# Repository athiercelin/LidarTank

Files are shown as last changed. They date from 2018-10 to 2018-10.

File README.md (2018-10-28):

# Lidar Tank

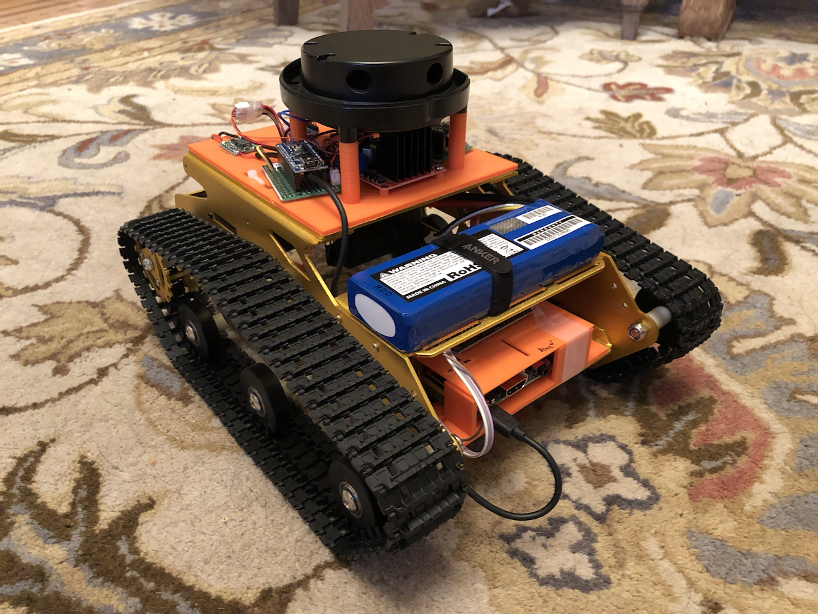
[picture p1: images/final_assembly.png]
Final Product


## Bill of Materials

|Quantity|Picture|Label|Comments|
|---|---|---|---|
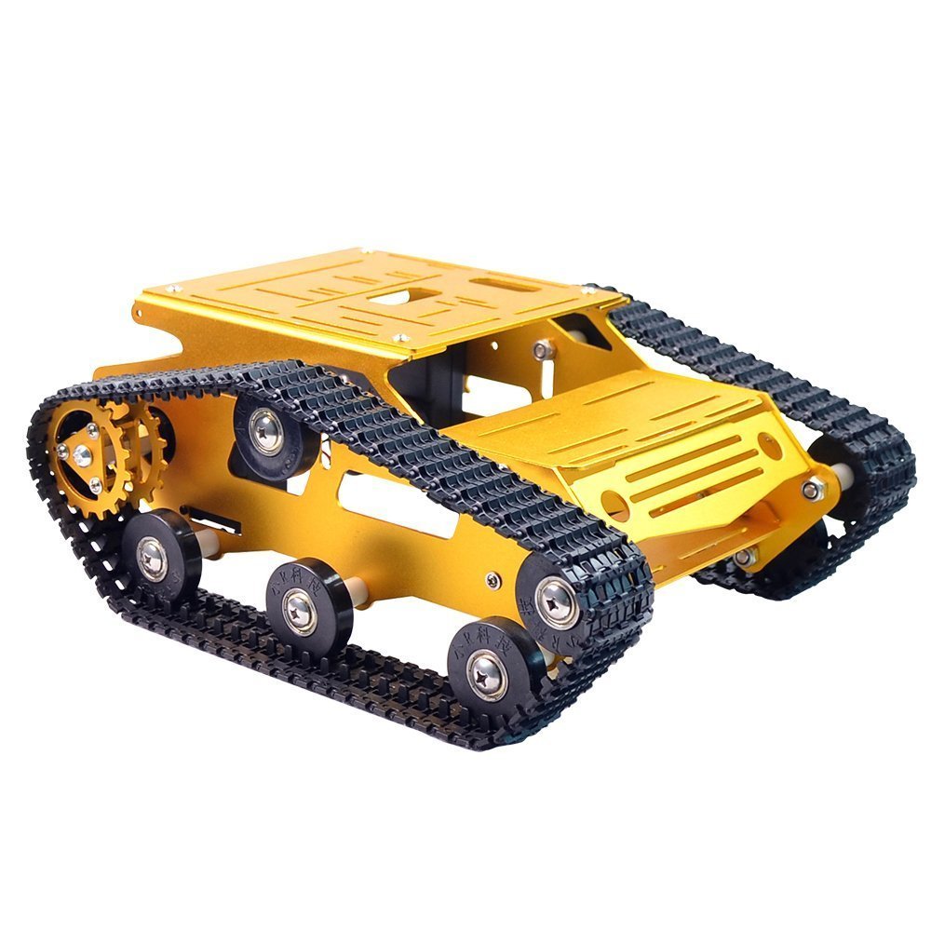
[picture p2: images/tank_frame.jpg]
|1||[Tank Frame](https://www.amazon.com/gp/product/B077Z4GYLB/ref=oh_aui_detailpage_o02_s00?ie=UTF8&psc=1)||
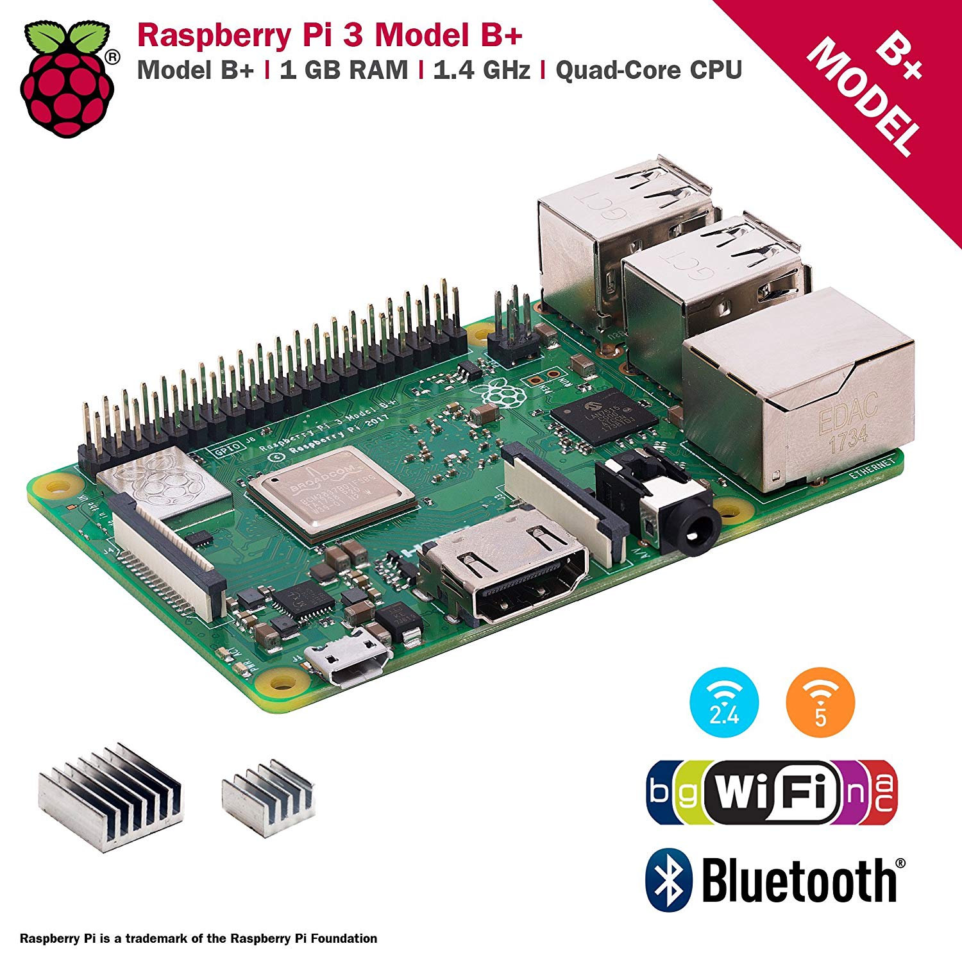
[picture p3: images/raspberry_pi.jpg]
|1||[Raspberry Pi 3+](https://www.amazon.com/gp/product/B07BC6WH7V/ref=oh_aui_detailpage_o02_s00?ie=UTF8&psc=1)||
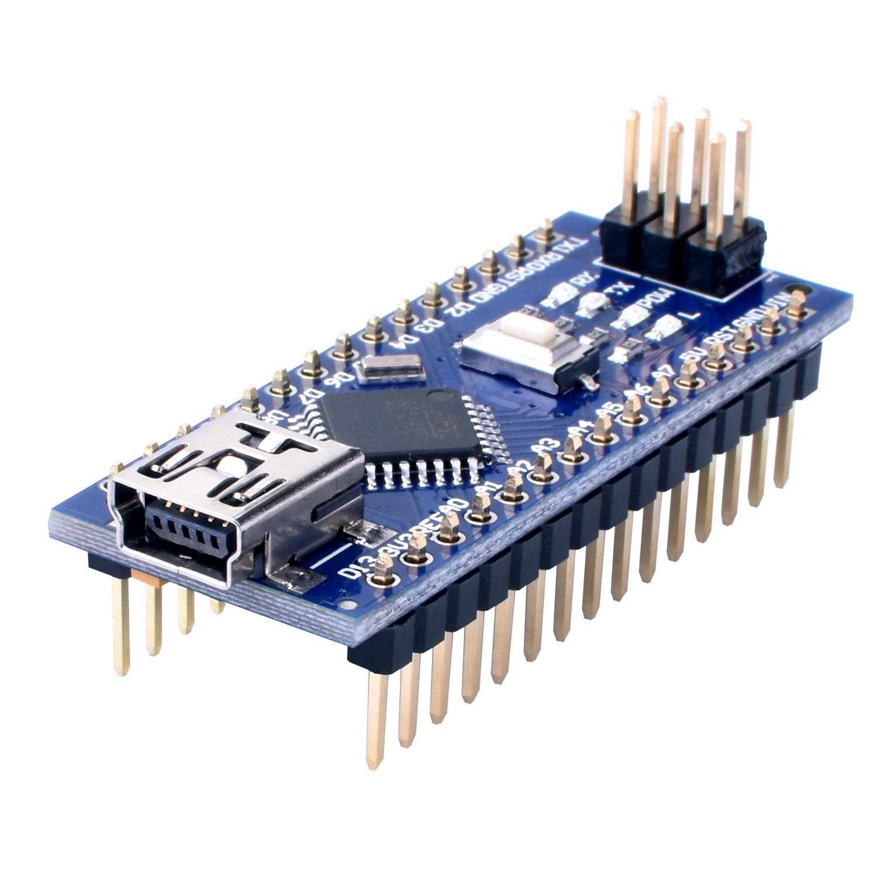
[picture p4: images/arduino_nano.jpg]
|2||[Arduino Nano](https://www.amazon.com/dp/B01MSYWE6B/ref=sspa_dk_detail_2?psc=1&pd_rd_i=B01MSYWE6B)|sd|
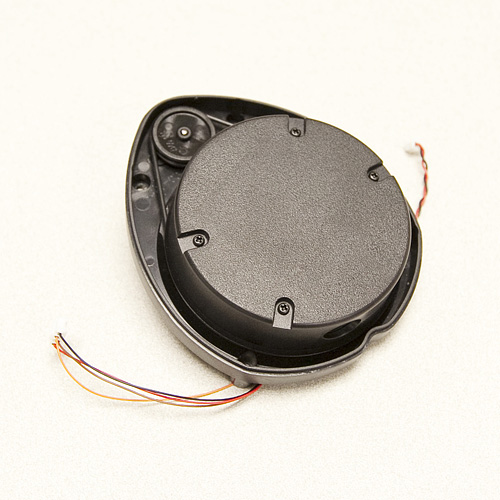
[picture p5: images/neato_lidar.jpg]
|1||Neato Lidar|I got this one for free so I don't have a place to find one easily|
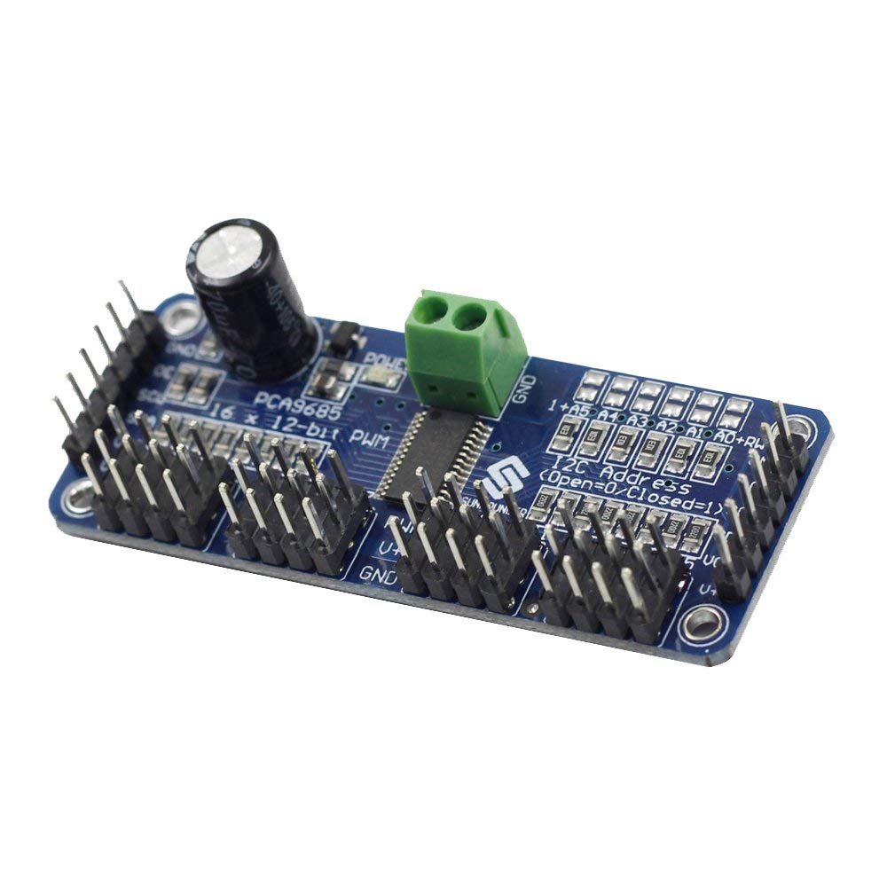
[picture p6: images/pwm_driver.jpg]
|1||[PWM Driver](https://www.amazon.com/gp/product/B014KTSMLA/ref=oh_aui_detailpage_o05_s00?ie=UTF8&psc=1)||
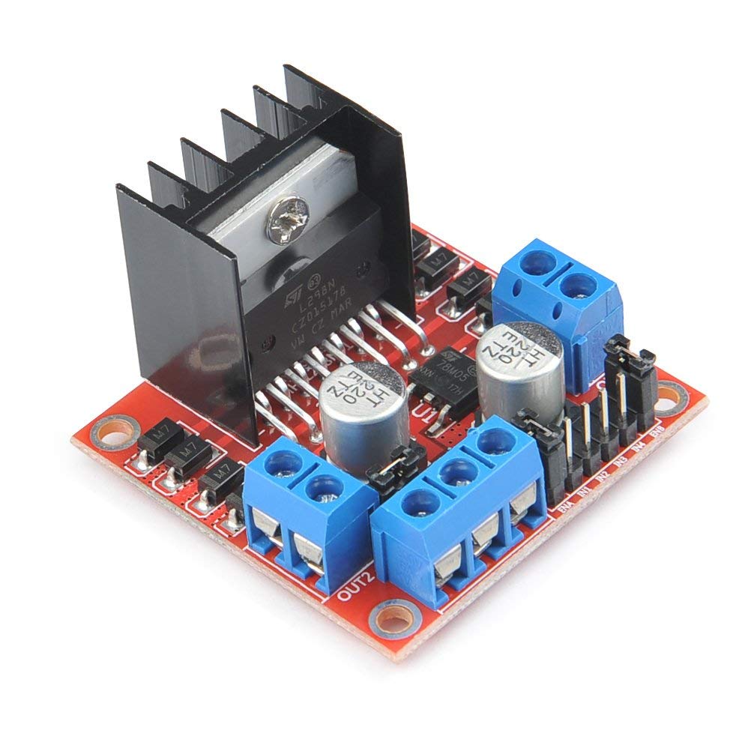
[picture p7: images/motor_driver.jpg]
|1||[Motor Driver](https://www.amazon.com/gp/product/B078D7DR9V/ref=oh_aui_detailpage_o05_s00?ie=UTF8&psc=1)||
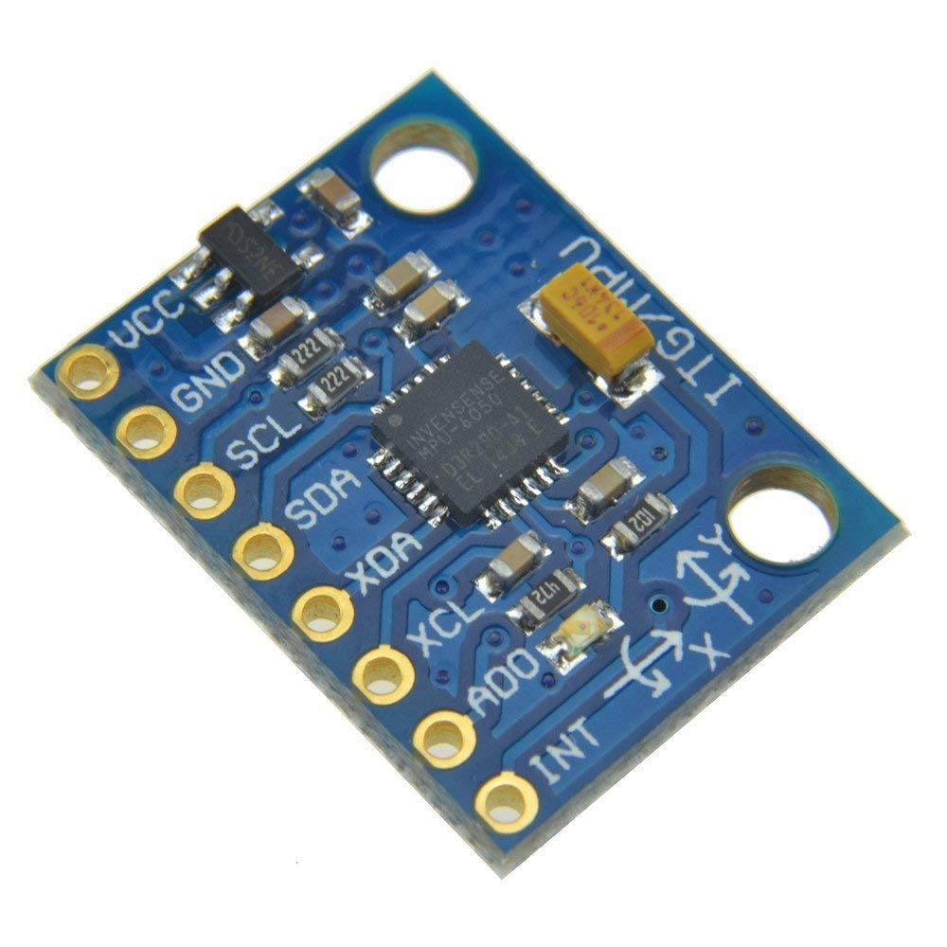
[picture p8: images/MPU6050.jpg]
|1||[MPU6050 IMU](https://www.amazon.com/Diymore-MPU-6050-Gyroscope-Accelerometer-Arduino/dp/B06XVXPZDP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)||
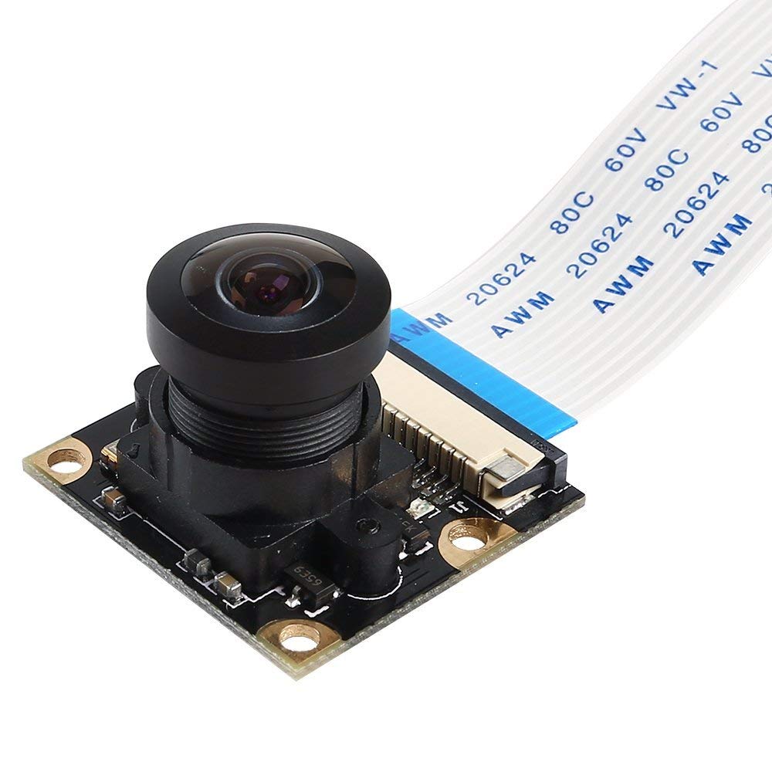
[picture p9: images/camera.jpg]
|1||[Camera module](https://www.amazon.com/gp/product/B00N1YJKFS/ref=oh_aui_detailpage_o00_s00?ie=UTF8&psc=1)||
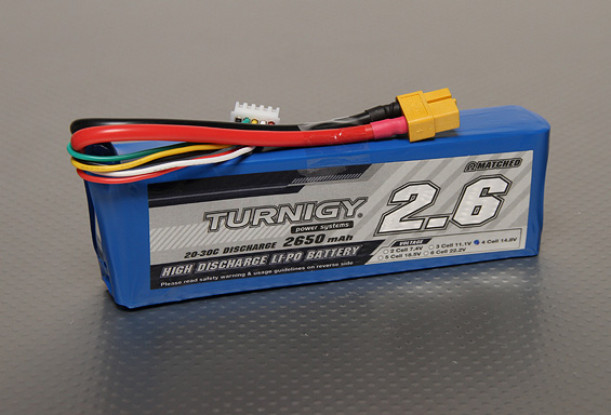
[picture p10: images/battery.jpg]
|1||[Battery](https://hobbyking.com/en_us/turnigy-2650mah-4s-20c-lipo-pack.html)||
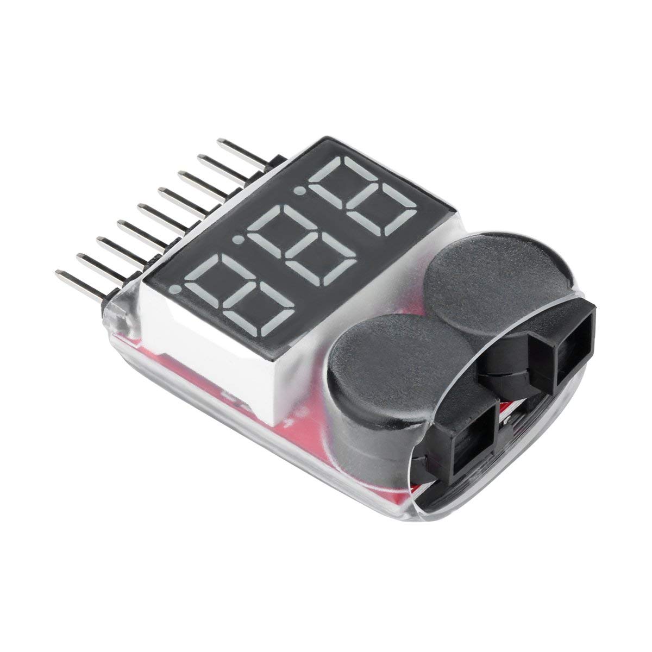
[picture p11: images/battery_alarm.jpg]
|1||[Battery Alarm](https://www.amazon.com/gp/product/B072JSLP66/ref=oh_aui_detailpage_o00_s01?)||
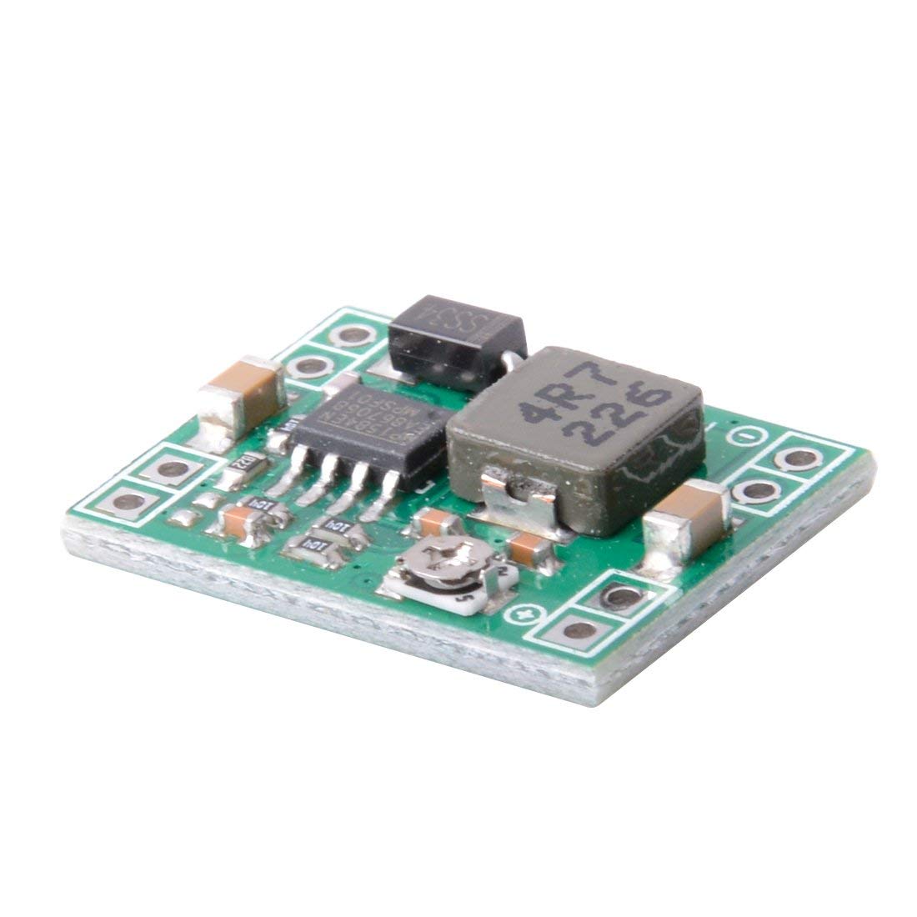
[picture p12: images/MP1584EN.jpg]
|2||[MP1584 Step Down](https://www.amazon.com/dp/B014Y3OT6Y/?coliid=I3SWYFK11098NR&colid=1QIA5LXOGB0GS&psc=0&ref_=lv_ov_lig_dp_it)|You can pick another one, you want 3A output at least on each. One will be set to output 12V, the other 5V.|
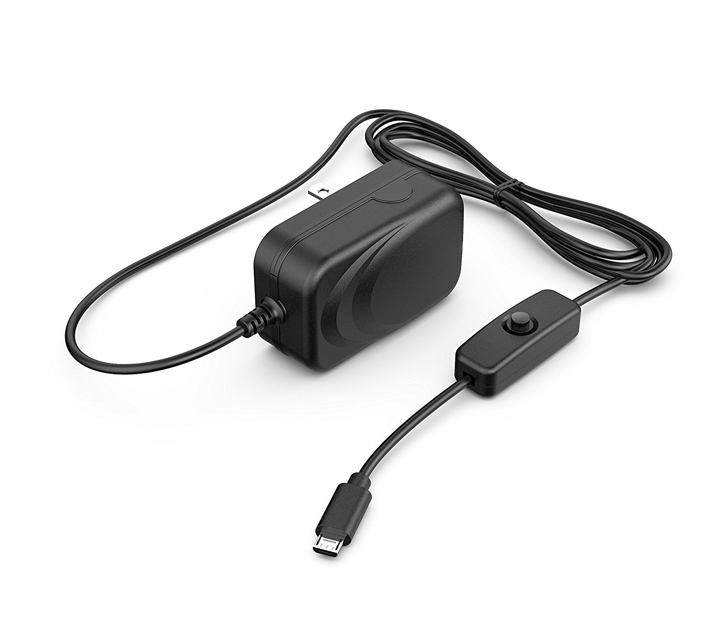
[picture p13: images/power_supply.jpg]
|1||[Power Supply](https://www.amazon.com/gp/product/B01N336XEU/ref=oh_aui_detailpage_o05_s00?ie=UTF8&psc=1)|The Raspberry Pi 3+ is more hungry and will need a more powerful USB power supply|

+ PS DS4 controller

## Notes
sudo apt-get install joystick

jstest /dev/input/js0

https://github.com/drewnoakes/joystick

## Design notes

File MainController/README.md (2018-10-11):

# Main Controller

The main controller is built on top of a Raspberry Pi 3 +

## Setup I2C

raspi-config

## Test I2C

i2ctools:
1/ i2cdetect
2/ i2cset
   i2cset -y 1 0x08 123

## PS4 Controller

ds4drv

https://github.com/chrippa/ds4drv

Read input from /dev/input

sudo apt-get install joystick
https://github.com/drewnoakes/joystick

## LAunching app at boot
@reboot /home/pi/Documents/LidarTank/bin/LidarTank &

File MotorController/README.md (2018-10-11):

# MotorController

Insert here protocol coming from I2C

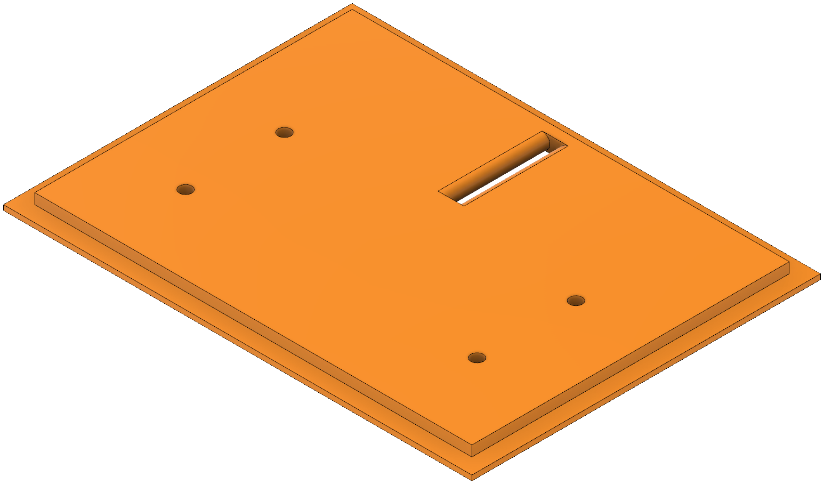
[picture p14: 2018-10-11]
images/bottom_control_cover.png

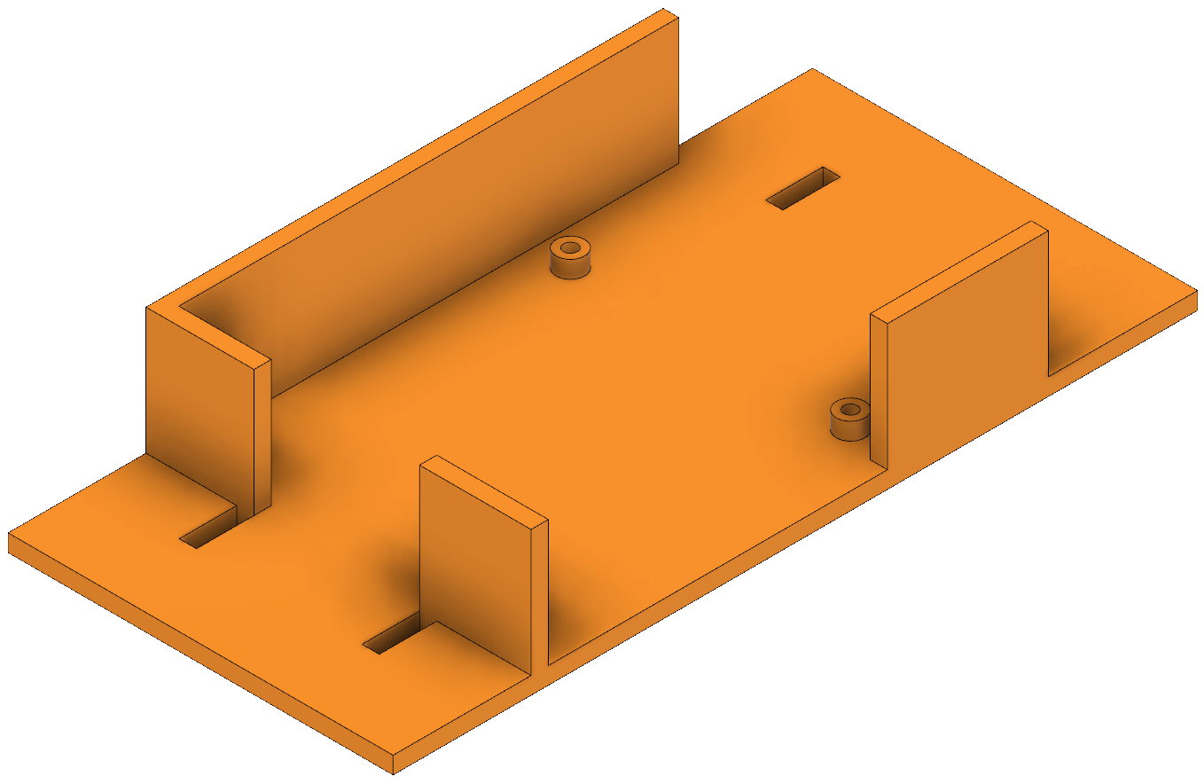
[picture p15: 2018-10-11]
images/bottom_control_case.png

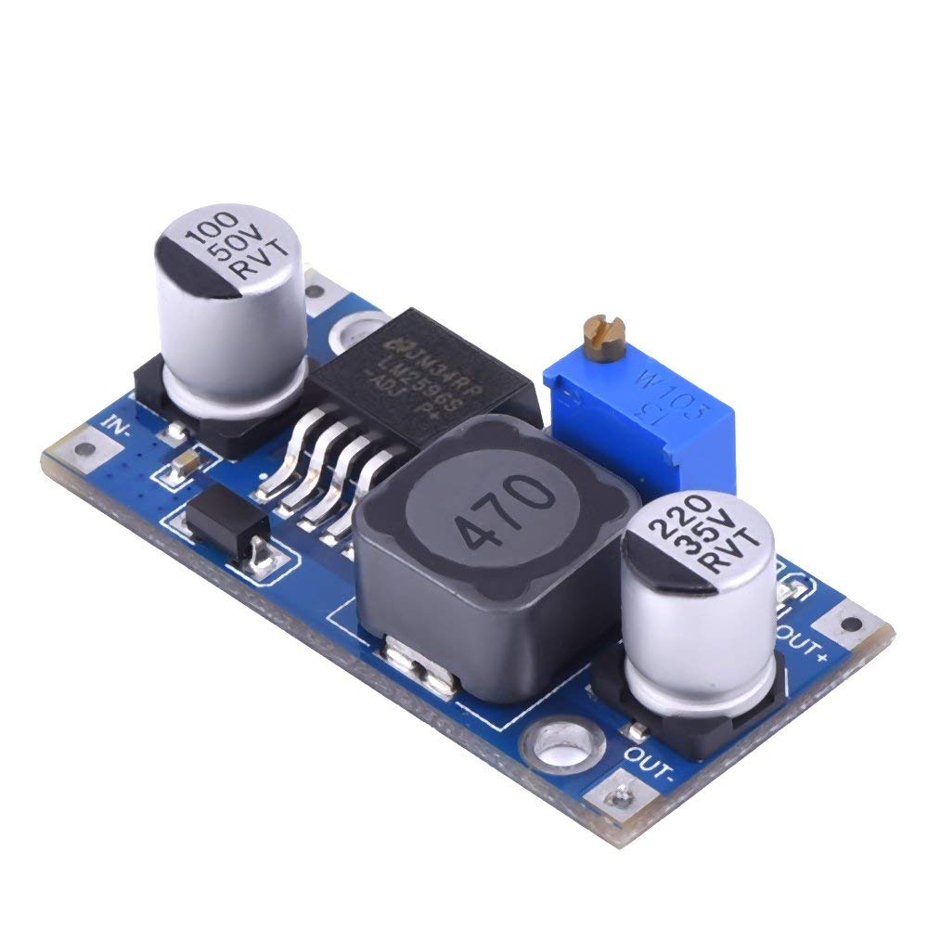
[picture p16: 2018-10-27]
images/LM2596.jpg

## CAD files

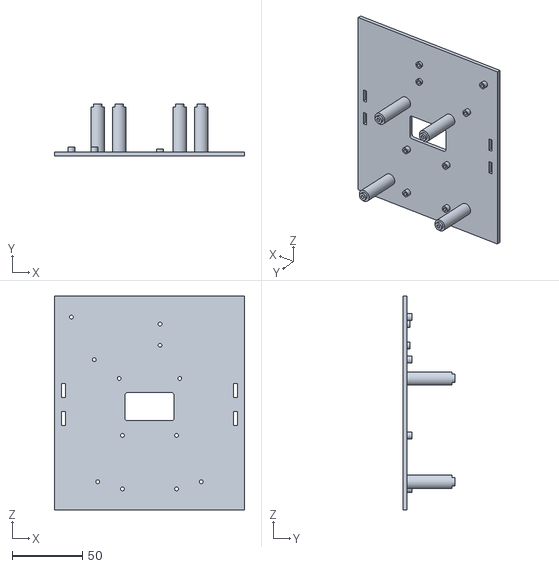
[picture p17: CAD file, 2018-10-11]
CAD/Top Control Plate v10.stl
135.0 x 37.0 x 152.0

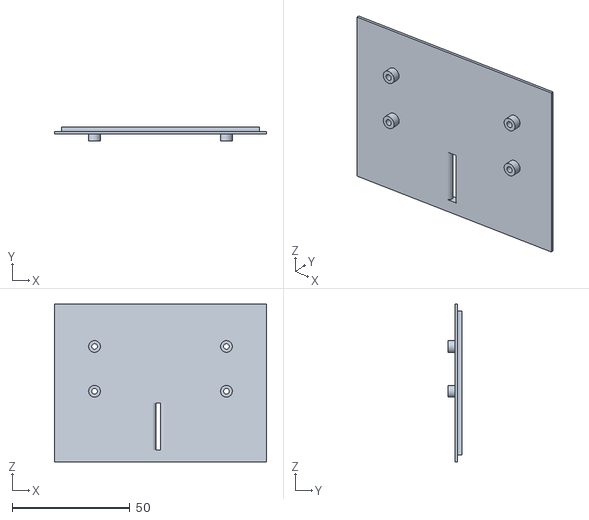
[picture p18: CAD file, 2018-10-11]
CAD/Bottom Control Cover v17.stl
90.0 x 6.00 x 67.0

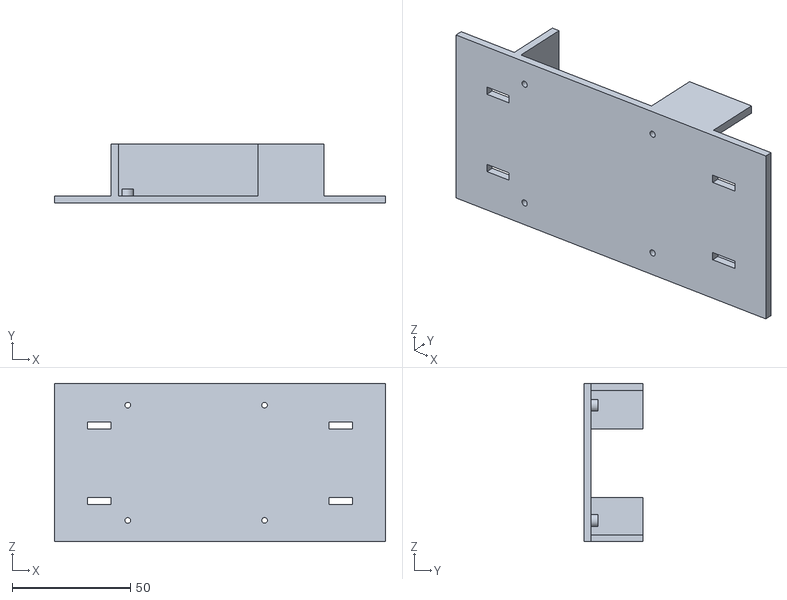
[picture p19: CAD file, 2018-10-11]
CAD/Bottom Control Case v5.stl
140.0 x 25.0 x 67.0

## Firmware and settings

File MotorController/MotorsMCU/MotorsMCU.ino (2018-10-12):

// 
//  Yellow Tank Robot v1.0
//  -- Motors controls through I2C by Raspberry pi --
//  Started: Oct 01, 2018
//  Author: Arnaud Thiercelin
//

#include <Wire.h>

// Left Motor
#define LEFTPIN1    4
#define LEFTPIN2    5
#define LEFTPWMPIN  6

// Right Motor
#define RIGHTPIN1   7
#define RIGHTPIN2   8
#define RIGHTPWMPIN 9

// Motor PWM settings
#define MOTOR_SLOWEST 100
#define MOTOR_FASTEST 255

// I2C

//
//  *** SETUP ***
//

void setup() {
  setupMotors();
  setupI2C();
  setupDebugging();
  Serial.println("Setup Complete - Motor Controls are ready!");
}

void setupMotors() {
  // Left Motor Pins
  pinMode(LEFTPIN1, OUTPUT);
  pinMode(LEFTPIN2, OUTPUT);
  pinMode(LEFTPWMPIN, OUTPUT);

  setLeftForward();

  // Right Motor Pins
  pinMode(RIGHTPIN1, OUTPUT);
  pinMode(RIGHTPIN2, OUTPUT);
  pinMode(RIGHTPWMPIN, OUTPUT);

  setRightForward();
}

void setupI2C() {
  Wire.begin(8);
  Wire.onReceive(receivedI2C);
  
}

void setupDebugging() {
  pinMode(LED_BUILTIN, OUTPUT);
  Serial.begin(9600);  
}

//
//  *** LOOP ***
//



void loop() {
 
  delay(100);
}

void motorTestLoop() {
   for (int pwm = MOTOR_SLOWEST; pwm < MOTOR_FASTEST; pwm++) {
    analogWrite(LEFTPWMPIN, pwm);
    analogWrite(RIGHTPWMPIN, pwm);
    Serial.print(pwm);
    Serial.print("\n");
    delay(5);
  }

  for (int pwm = MOTOR_FASTEST; pwm >= MOTOR_SLOWEST - 30 ; pwm--) {
    analogWrite(LEFTPWMPIN, pwm);
    analogWrite(RIGHTPWMPIN, pwm);
    Serial.print(pwm);
    Serial.print("\n");
    delay(5);
  }



// After once, we stop
    analogWrite(LEFTPWMPIN, 0);
    analogWrite(RIGHTPWMPIN, 0);
    
    while (1) {
      digitalWrite(LED_BUILTIN, HIGH);   // turn the LED on (HIGH is the voltage level)
      delay(500);                       // wait for a second
      digitalWrite(LED_BUILTIN, LOW);    // turn the LED off by making the voltage LOW
      delay(500);
    } 
}

//
//  *** I2C ***
//

void receivedI2C() {
    Serial.println("---");
    while (Wire.available()) {
      // Read commands
      int data = Wire.read();

      Serial.print("I2C Received: ");
      Serial.println(data);
      handleMotorCommand(data);
    }
    Serial.println("Done Reading");
}

//
//  *** MOTORS FUNCTIONS ***
//

// LEFT MOTORS

void handleMotorCommand(int i2cValue) {
// Commands are defined as such.
// - Values sent are between [0, 200]
// - Values are then mapped to [-100, 100]
// - Positive values means forwards
// - Negative values means bacwards
// - Odd values means Left
// - Even values means Right

  if (i2cValue == 0) {
    return;
  }

  int commandValue = i2cValue - 100;
  Serial.print("Command Receive: ");
  Serial.println(commandValue);

  if (commandValue == 0) {
    setLeftSpeed(0);
    setRightSpeed(0);
    Serial.println("Stopping");
  } else if (commandValue % 2) {
    Serial.print("Activating Left");
    if (commandValue > 0) {
      setLeftForward();
      setLeftSpeed(abs(commandValue));
      Serial.println(" Forward");
    } else {
      setLeftBackward();
      setLeftSpeed(abs(commandValue));
      Serial.println (" Backward");
    }
  } else {
    Serial.print("Activating Right");
    if (commandValue > 0) {
      setRightForward();
      setRightSpeed(abs(commandValue));
      Serial.println(" Forward");
    } else {
      setRightBackward();
      setRightSpeed(abs(commandValue));
      Serial.println (" Backward");
    }
  }
}

void setLeftSpeed(int speedValue) {
  static int currentSpeed = 0;
  int pwm = currentSpeed;
  
  if (speedValue == 0) {
    pwm = 0;    
  } else {
    pwm = map(speedValue, 0, 200, MOTOR_SLOWEST, MOTOR_FASTEST);
  }
//  for (int pwm = MOTOR_SLOWEST; pwm < MOTOR_FASTEST; pwm++) {
    analogWrite(LEFTPWMPIN, pwm);
    Serial.print("Left Speed: ");
    Serial.println(pwm);
//    delay(5);
//  }

  currentSpeed = pwm;
}

void setLeftForward() {
  digitalWrite(LEFTPIN1, HIGH);
  digitalWrite(LEFTPIN2, LOW);
}

void setLeftBackward() {
  digitalWrite(LEFTPIN1, LOW);
  digitalWrite(LEFTPIN2, HIGH);
}

// RIGHT MOTORS

void setRightSpeed(int speedValue) {
  static int currentSpeed = 0;
  int pwm = currentSpeed;
  
  if (speedValue == 0) {
    pwm = 0;    
  } else {
    pwm = map(speedValue, 0, 200, MOTOR_SLOWEST, MOTOR_FASTEST);
  }
//  for (int pwm = MOTOR_SLOWEST; pwm < MOTOR_FASTEST; pwm++) {
    analogWrite(RIGHTPWMPIN, pwm);
    Serial.print("Right Speed: ");
    Serial.println(pwm);
//    delay(5);
//  }

  currentSpeed = pwm;
}

void setRightForward() {
  digitalWrite(RIGHTPIN1, HIGH);
  digitalWrite(RIGHTPIN2, LOW);
}

void setRightBackward() {
  digitalWrite(RIGHTPIN1, LOW);
  digitalWrite(RIGHTPIN2, HIGH);
}

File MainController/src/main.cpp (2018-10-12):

//
//  Project: Lidar Tank
//  main.cpp
//  Author: Arnaud Thiercelin
//  Date Created: 2018-10-10
// 

#include "main.hpp"

int main(int argc, char** argv)
{

  //
  //  Init the Controller
  //

  std::string devicePath("/dev/input/js0");

  printf("Initialize Remote Controller\n");
  Joystick *joystick = NULL;
  
  while (true) {
  
    // Create an instance of Joystick
    joystick = new Joystick(devicePath);

    if (!joystick->isFound())
    {
      printf("Failed finding joystick device. Will try again in 2s\n");
      delete joystick;
      sleep(2);
    } else {
      break;
    }
  }

  printf("*** Remote Controller ready!\n");
  
  //
  //  I2C/GPIO setup
  //

  printf("Initializing I2C\n");
  
  wiringPiSetupGpio();
  int motorMCUfd = wiringPiI2CSetup(0x08);
  if (motorMCUfd < 0)
    {
      std::cout << "I2C Setup Error" << std::endl;
      return 0;
    }

  printf("*** I2C ready!\n");

  //
  //  Main Loop
  //
  
  while (true)
    {
      // Restrict rate
      usleep(1000); // original value 1000

      // Attempt to sample an event from the joystick
      JoystickEvent event;
      if (joystick->sample(&event))
	{
	  if (event.isButton()) {
	    if (event.number == 0) {
	      printf("Button %u is %s\n",
		     event.number,
		     event.value == 0 ? "up" : "down");
	      wiringPiI2CWrite(motorMCUfd, 100);
	    }
	  } else if (event.isAxis()) {
	    int axisNumber = event.number;

	    // Neg value means pushed forward on stick axis 1 and 4
	    // Positive value means pulled back.
	    printf("Axis %u is at position %d\n", event.number, event.value);
	
	    if (axisNumber == 1) { // Left Stick
	      static int command = 100; // 0
	      int newCmd = 0;

	      newCmd = leftAxisPercentageToCommand(axisEventValueToPercentage(&event));
	      
	      if (newCmd != command) {
		printf("I2C Sending %d\n", newCmd);

		// TODO: This needs a throttling, 5-10Hz
		while (wiringPiI2CWrite(motorMCUfd, newCmd) != 0) {
		  usleep(1000);
		}
		command = newCmd;

	      } else {
		//	printf("OLD: [%d] NEW: [%d]\n", command, newCmd);
	      }
	  
	    }
	    if (axisNumber == 4) { // Right Stick
	      static int command = 100; // 0
	      int newCmd = 0;
	 
	      newCmd = rightAxisPercentageToCommand(axisEventValueToPercentage(&event));

	      if (newCmd != command) {
		printf("I2C Sending %d\n", newCmd);

		// TODO: This needs a throttling, 5-10Hz
		while (wiringPiI2CWrite(motorMCUfd, newCmd) != 0) {
		  usleep(1000);
		}
		command = newCmd;
		
	      } else {
		//	printf("OLD: [%d] NEW: [%d]\n", command, newCmd);
	      }
	
	    }
	  }
	}
    }
}


int axisEventValueToPercentage(JoystickEvent *event) {

  int eventValue = event->value;
  int percentage = 0;

  if (eventValue > 0) {
    percentage = -1 * ((float)eventValue / (float)event->MAX_AXES_VALUE) * 100;
    // printf("EventVal: %d, [%d] Percentage: %d\n", eventValue, event->MAX_AXES_VALUE, percentage);
  } else if (eventValue < 0) {
    percentage = ((float) eventValue / (float)event->MIN_AXES_VALUE) * 100;
    // printf("EventVal: %d, [%d] Percentage: %d\n", eventValue, event->MIN_AXES_VALUE, percentage);
  }

  // Filter
  if (percentage > -10 && percentage < 10) {
    percentage = 0;
  }
  return percentage; 
}

int leftAxisPercentageToCommand(int percentage) {
  int command = percentage + 100;

  if (!(command % 2) && command != 100) {
    if (command == 200) {
      command--;
    } else {
      command++;
    }
  }     
  
  return command;
}

int rightAxisPercentageToCommand(int percentage) {
  int command = percentage + 100;
  
  if (command % 2 && command != 100) {
    if (command != 200) {
      command++;
    } else {
      command--;
    }
  }     
  
  return command;
}

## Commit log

2018-10-11 Added STL + pics
    Added the ino for moto controls
    [Battery Holder v15.stl, Bottom Control Case v5.stl, Bottom Control Cover v17.stl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]
2018-10-12 Modified the I2C data send, but it needs some throttling and identifying the 16 command passed by error.
    [main.cpp]
2018-10-12 Minor tweak in motor controller code.
2018-10-27 Cleaned up the README
    [Battery Holder v15.stl]
